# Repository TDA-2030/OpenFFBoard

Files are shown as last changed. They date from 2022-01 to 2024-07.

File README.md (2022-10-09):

# OpenFFBoard-ESP32S2 + VESC

这里将介绍使用 ESP32-S2/S3 版本的 OpenFFBoard 搭配自制 VESC 驱动器使用的一个低成本实现直驱力反馈方向盘方案。[OpenffBoard](https://github.com/Ultrawipf/OpenFFBoard) 是一个开源的力反馈方向盘的项目，整个项目硬件分为 `控制板` 和 `电机驱动板` 两个部分，这里对两个部分都进行了低成本方向的修改。

## 文件结构

```
├── LICENSE                <- 开源协议 >
├── Simple-BLDC            <- 电机驱动板 >
├── openffboard-esp32s2    <- OpenFFBoard 主控板 >
├── Structural_parts       <- 一些可能有帮助的结构件>
└── README.md              <- 此文件 >
```

## OpenFFBoard-ESP32S2 控制板

原项目控制板是 STM32F4 做主控，这里将主控换成了[乐鑫](https://www.espressif.com/zh-hans)的 ESP32-S2/S3 芯片，成本得到极大的降低，同时提供了 WiFi 的连接能力（虽然现在并没有用上）。硬件开源资料见 [openffboard-esp32s2](./openffboard-esp32s2)

> V1.1 版本的硬件支持 ESP32-S2 和 ESP32-S3 二选一焊接，下文统称为 ESP32

和原项目相比，ESP32 不能提供足够多的 GPIO ，所以按键输入和模拟输入通道数均从原来的 8 通道精简到了 4 通道。详细信息见原理图 [esp32s2-openffb.pdf](openffboard-esp32s2/esp32s2-openffb.pdf)。
ESP32 控制板的源码已提交 Pull Request 到原项目，支持的功能以及进度见 [PR](https://github.com/Ultrawipf/OpenFFBoard/pull/46)。

### 控制板固件烧录

参见[快速下载固件指南](https://github.com/TDA-2030/OpenFFBoard/tree/feature/add_esp32s2/Firmware/Targets/ESP32SX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)

## 电机驱动板

为了造福广大劳动人民，针对原项目的电机驱动我也进行了低成本的改造，原项目是采用了比较贵的 TMC4761 专用 FOC 控制芯片，我将著名的开源电调 [VESC](https://vesc-project.com/) 进行了魔改，去掉了昂贵的 DRV8301 芯片，用多个芯片实现了这一个芯片的功能。集成度下降了，但是价格更友好。魔改后的 VESC 我叫它 `Simple-BLDC` 。关于电机驱动板的更多信息见 [Simple-BLDC](Simple-BLDC/README.md)

## 组装好的样子

assembly

## 测试工具

[WheelTest](./WheelTest.rar) 提供了一个测试力反馈功能是否正常的软件

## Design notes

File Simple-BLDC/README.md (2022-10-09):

# Simple-BLDC

```
 _____ _                 _       ______ _    ______  _____ 
/  ___(_)               | |      | ___ \ |   |  _  \/  __ \
\ `--. _ _ __ ___  _ __ | | ___  | |_/ / |   | | | || /  \/
 `--. \ | '_ ` _ \| '_ \| |/ _ \ | ___ \ |   | | | || |    
/\__/ / | | | | | | |_) | |  __/ | |_/ / |___| |/ / | \__/\
\____/|_|_| |_| |_| .__/|_|\___| \____/\_____/___/   \____/
                  | |                                      
                  |_|                                      
```

Simple-BLDC 是基于 VESC6 的一个低成本实现方案，在硬件上兼容 VESC6 的固件

## 特点

- 超低成本
- 60mm x 60mm 双面板
- 元件单面布局
- 新增制动电阻功能
- USB Type-C 接口

## 参数

1. 输入电压：12V - 36V
2. 电机电流：50A
3. 编码器支持：AS5047（SPI接口）、ABI编码器
4. 通信接口：CAN总线接口、UART

## 固件源码

板子兼容[原版固件](https://github.com/vedderb/bldc)，专门适配的固件新增了制动电阻功能，你可以在 [bldc](https://github.com/TDA-2030/bldc/tree/hw_simple_bldc) 中看到对应的源代码。如何编译固件请参考[这里](https://github.com/TDA-2030/bldc/tree/hw_simple_bldc#prerequisites)，目前只提供在 linux 和 MacOS 编译的说明，Windows 编译会麻烦一些需要自行想办法。

## 上位机工具 VESC-TOOL

固件对应的 VESC-TOOL 版本为 `3.01`，在此[下载](./vesc_tool_3.01.exe)

## 制动电阻功能

原版的 VESC 是为电池设备设计的，所以是再生制动的方式，为了适应常见的开关电源，我加上了制动电阻来消耗再生制动的能量，防止开关电源超压损坏。
该功能需要在板子背面焊接上一个功率电阻，如下图：

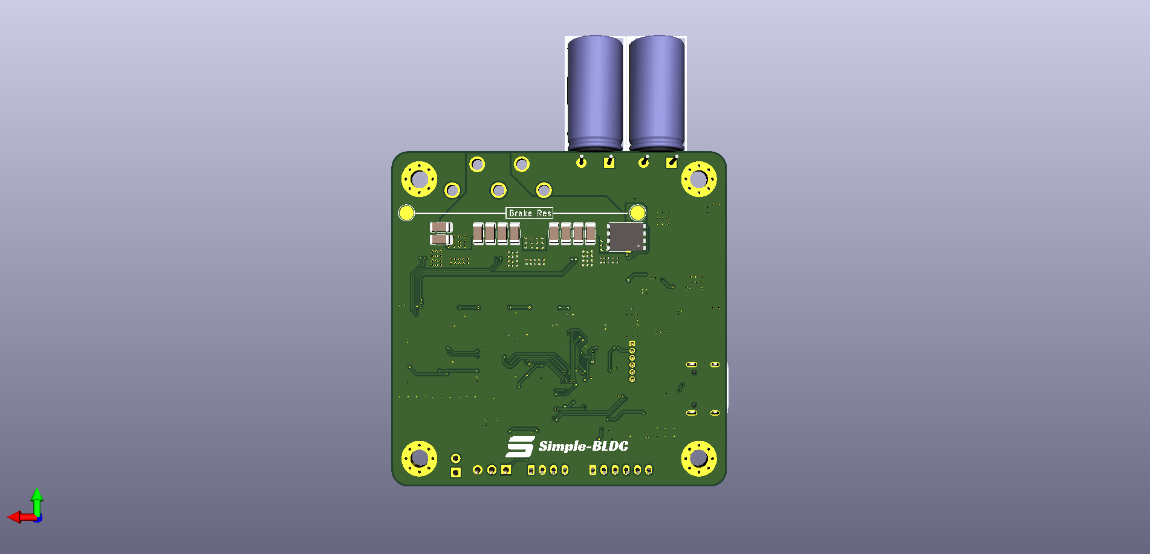
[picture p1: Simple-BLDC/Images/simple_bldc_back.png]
simple_bldc_back


电阻阻值一般为 1Ω 或 2Ω。

> 注意：制动电阻功能是在有点笨的保持电压在电机空闲时的输入电压，所以当电机在运行，并且你的输入电压在升高，那么制动电阻将会从电源消耗电流，电流值与变化的电压差值成正比。

制动电阻功能可以在 VESC-TOOL 进行开关选择，如下图：

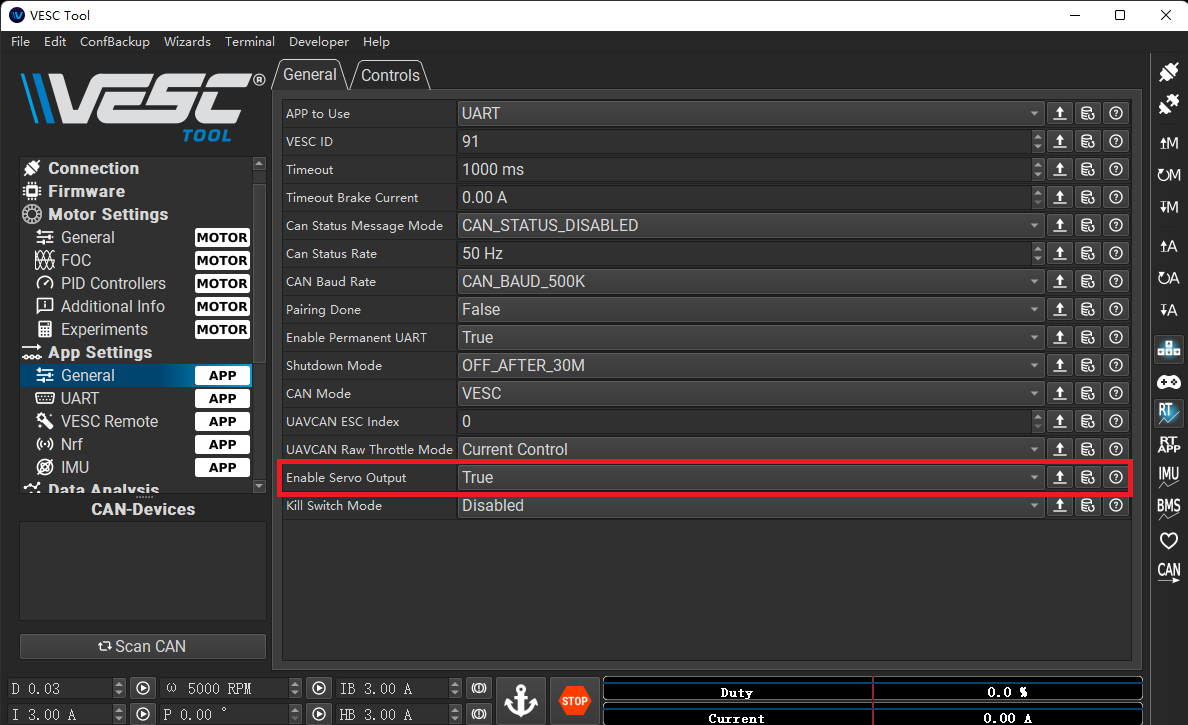
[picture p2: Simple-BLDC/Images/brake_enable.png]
brake_enable


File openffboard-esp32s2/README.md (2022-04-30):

## Preview image

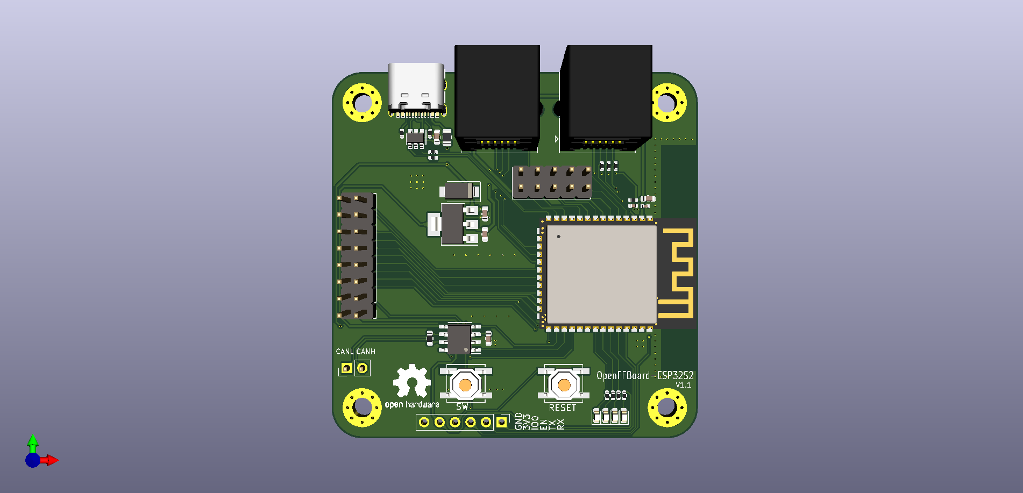
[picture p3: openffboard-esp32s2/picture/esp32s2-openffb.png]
front


## Known issues

The silk screen of the two buttons is wrong

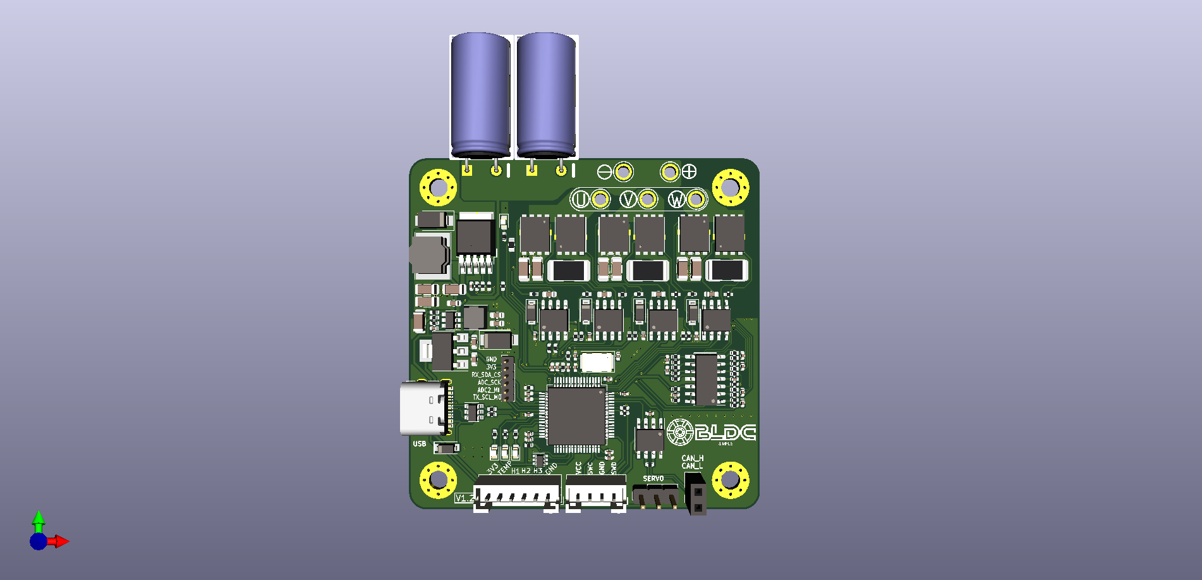
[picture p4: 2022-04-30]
Simple-BLDC/Images/simple_bldc.png

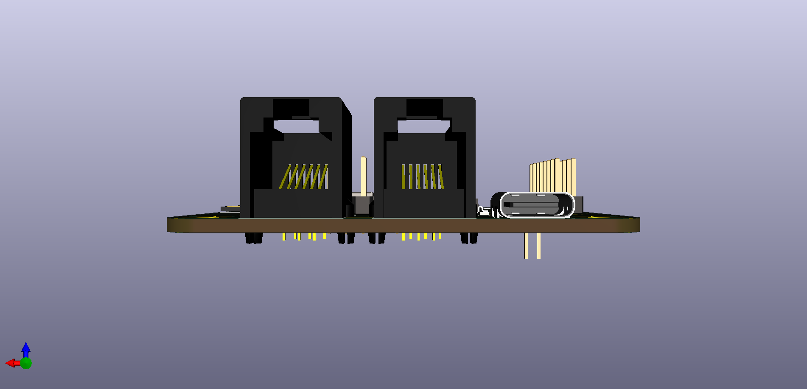
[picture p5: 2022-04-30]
openffboard-esp32s2/picture/connector.png

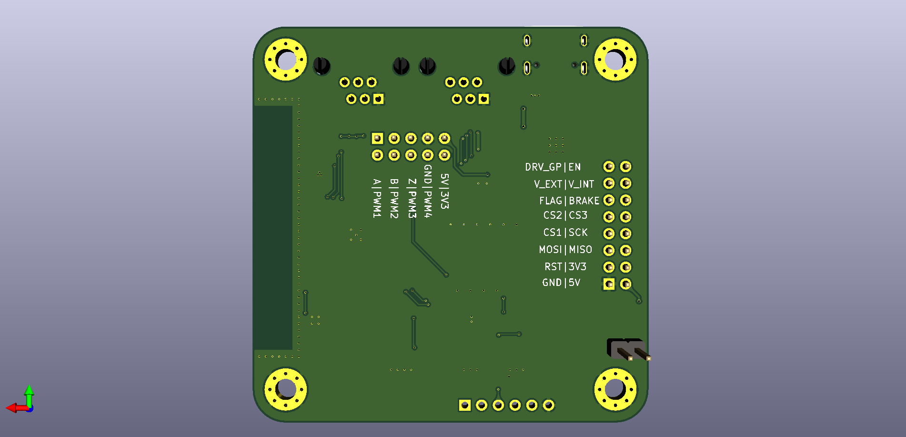
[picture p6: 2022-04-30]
openffboard-esp32s2/picture/back.png

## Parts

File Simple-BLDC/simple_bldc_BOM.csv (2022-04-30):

Comment | Description | Designator | Footprint | LibRef | Pins | Quantity | PartNumber | url
100n | desc | C1,C4,C5,C9,C15,C37,C45, | C_0402_1005Metric | libref | 2 | 7
2.2u | desc | C3,C20,C22,C26,C33,C34,C36,C38,C40,C41,C42,C43,C44,C63, | C_0402_1005Metric | libref | 2 | 14
10uf | desc | C6,C10,C11,C16,C17, | C_0603_1608Metric | libref | 2 | 5
10uF, 50V | desc | C7,C29,C30,C31,C46,C47,C48, | C_1206_3216Metric | libref | 2 | 7
1nF | desc | C8,C13,C18,C19,C23,C24, | C_0402_1005Metric | libref | 2 | 6
22uF, 25V | desc | C12,C14,C60, | C_1206_3216Metric | libref | 2 | 3
220n | desc | C21,C25,C27,C64, | C_0603_1608Metric | libref | 2 | 4
15p | desc | C35,C39, | C_0402_1005Metric | libref | 2 | 2
33nF | desc | C50, | C_0402_1005Metric | libref | 2 | 1
B5819W | desc | D1,D6,D7,D8,D11, | D_SOD-123 | libref | 2 | 5
RED | desc | D2, | LED_0603_1608Metric | libref | 2 | 1
GREEN | desc | D3, | LED_0603_1608Metric | libref | 2 | 1
BLUE | desc | D4, | LED_0603_1608Metric | libref | 2 | 1
SS210 | desc | D5, | D_SMA | libref | 2 | 1
SMAJ5.0CA_400W_5V | desc | D10, | D_SMA | libref | 2 | 1
LED_RED | desc | D12, | LED_0603_1608Metric | libref | 2 | 1
Logo | desc | H9, | simple-bldc-logo1 | libref | 0 | 1
6.8uH | desc | L1, | L_Taiyo-Yuden_NR-40xx | libref | 2 | 1
100uH | desc | L2, | L_Taiyo-Yuden_NR-60xx_HandSoldering | libref | 2 | 1
BSC030N08NS5 | desc | Q1,Q2,Q3,Q4,Q5,Q6, | DFN5_5x6_1.27P_(SO-8FL) | libref | 10 | 6
2k2 | desc | R1,R3,R6,R19,R37,R39,R41, | R_0402_1005Metric | libref | 2 | 7
120k | desc | R2,R21, | R_0402_1005Metric | libref | 2 | 2
10R | desc | R4,R42,R43,R45,R46,R48,R49, | R_0402_1005Metric | libref | 2 | 7
39k | desc | R5,R36,R38,R40, | R_0402_1005Metric | libref | 2 | 4
22R | desc | R7,R8, | R_0402_1005Metric | libref | 2 | 2
1k | desc | R9,R10,R11,R16,R23,R24,R25,R26,R32,R33,R34,R35,R57, | R_0402_1005Metric | libref | 2 | 13
120R | desc | R12,R52,R56, | R_0402_1005Metric | libref | 2 | 3
10k | desc | R13,R14,R15,R51,R55, | R_0402_1005Metric | libref | 2 | 5
22k | desc | R17, | R_0402_1005Metric | libref | 2 | 1
20k | desc | R18,R20,R22,R27,R28,R29,R30,R31, | R_0402_1005Metric | libref | 2 | 8
0.001R | desc | R44,R47,R50, | R_2512_Yageo_big_pads | libref | 2 | 3
MCP6024 | desc | U1, | SOIC-14_3.9x8.7mm_P1.27mm | libref | 14 | 1
MP1471 | desc | U2, | SOT-23-6 | libref | 6 | 1
XL7015 | desc | U3, | TO-252-5_TabPin3 | libref | 10 | 1
AMS1117-3.3 | desc | U4, | SOT-223-3_TabPin2 | libref | 4 | 1
IRS2101S | desc | U5,U6,U7,U11, | SOIC-8_3.9x4.9mm_P1.27mm | libref | 8 | 4
STM32F40X_LQFP64 | desc | U8, | LQFP-64_10x10mm_P0.5mm | libref | 64 | 1
TJA1051T-3 | desc | U9, | SOIC-8_3.9x4.9mm_P1.27mm | libref | 8 | 1
USBLC6-2SC6 | desc | U10, | SOT-23-6 | libref | 6 | 1
PESD3V3L5UY | desc | U12, | SOT-363_SC-70-6 | libref | 6 | 1
8MHz 10ppm (X50328MSB2GI) | desc | X1, | Crystal_SMD_5032-2Pin_5.0x3.2mm | libref | 2 | 1
Net-Tie_2 | desc | NT1,NT2,NT3,NT4,NT5,NT6, | NetTie-2_SMD_Pad0.5mm | libref | 2 | 6
NTC 10k | desc | NTC1, | R_0603_1608Metric | libref | 2 | 1
10uF, 50V | desc | C2,C49,C51,C52,C53,C54,C55,C57,C58,C59, | C_1206_3216Metric | libref | 2 | 10
Logo | desc | H5, | simple-bldc-logo3 | libref | 0 | 1
NTMFS4C08N | desc | Q7, | DFN5_5x6_1.27P_(SO-8FL) | libref | 10 | 1
POS | desc | RES1,RES2, | TestPoint_Pad_D2.5mm | libref | 1 | 2
Through Hole Items
330u, 63V | desc | C28,C32, | CP_10x20mm_hor_with_model_brd_edge | libref | 2 | 2
MountingHole_Pad | desc | H1,H2,H3,H4, | MountingHole_3.2mm_M3_Pad_Via | libref | 9 | 4
Conn_01x03 | desc | J1, | PinHeader_1x03_P2.54mm_Vertical | libref | 3 | 1
USB_C_Receptacle_USB2.0 | desc | J2, | USB_C_Receptacle_Palconn_UTC16-G | libref | 22 | 1
CAN | desc | J3, | PinSocket_1x02_P2.54mm_Vertical | libref | 2 | 1
Conn_01x06 | desc | J4, | PinHeader_1x06_P1.27mm_Vertical | libref | 6 | 1
SWD | desc | J6, | JST_PH_B4B-PH-K_1x04_P2.00mm_Vertical | libref | 4 | 1
HALL/Encoder | desc | P1, | JST_PH_B6B-PH-K_1x06_P2.00mm_Vertical | libref | 6 | 1
MOTOR1 | desc | P2,P3,P4, | 1pin_2mm | libref | 1 | 3
MOTOR3 | desc | NEG1, | 1pin_2mm | libref | 1 | 1
POS | desc | POS1, | 1pin_2mm | libref | 1 | 1

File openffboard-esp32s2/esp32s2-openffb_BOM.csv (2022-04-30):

Comment | Description | Designator | Footprint | LibRef | Pins | Quantity | PartNumber | url
10uf | desc | C1,C2,C3,C4,C19, | C_0603_1608Metric | libref | 2 | 5
0.1uf | desc | C6,C15, | C_0402_1005Metric | libref | 2 | 2
SMAJ5.0CA_400W_5V | desc | D1, | D_SMA | libref | 2 | 1
blue | desc | D9, | LED_0603_1608Metric | libref | 2 | 1
yellow | desc | D10, | LED_0603_1608Metric | libref | 2 | 1
red | desc | D11, | LED_0603_1608Metric | libref | 2 | 1
green | desc | D12, | LED_0603_1608Metric | libref | 2 | 1
500mA | desc | F1, | Fuse_0805_2012Metric | libref | 2 | 1
22Ω | desc | R1,R2, | R_0402_1005Metric | libref | 2 | 2
10k | desc | R4, | R_0402_1005Metric | libref | 2 | 1
5.1k | desc | R5,R10,R11,R12,R13, | R_0402_1005Metric | libref | 2 | 5
1k | desc | R6,R7,R8,R9, | R_0402_1005Metric | libref | 2 | 4
120Ω | desc | R15, | R_0603_1608Metric | libref | 2 | 1
AMS1117-3.3 | desc | U1, | SOT-223-3_TabPin2 | libref | 4 | 1
ESP32-S3-WROOM-1 | desc | U2, | ESP32-S3-WROOM-1 | libref | 49 | 1
TJA1051T-3 | desc | U3, | SOIC-8_3.9x4.9mm_P1.27mm | libref | 8 | 1
USBLC6-2SC6 | desc | U4, | SOT-23-6 | libref | 6 | 1
ESP32-S2-SOLO | desc | U5, | ESP32-S2-SOLO | libref | 49 | 1
SW_Push | desc | SW1,SW2, | SW_SPST_EVPBF | libref | 4 | 2
logo | desc | logo1, | OSHW-Logo2_9.8x8mm_SilkScreen | libref | 0 | 1
Through Hole Items
MountingHole_Pad | desc | H1,H2,H3,H4, | MountingHole_3.2mm_M3_Pad_Via | libref | 9 | 4
USB_C_Receptacle_USB2.0 | desc | J1, | USB_C_Receptacle_Palconn_UTC16-G | libref | 22 | 1
Debug | desc | J2, | PinHeader_1x06_P2.54mm_Vertical | libref | 6 | 1
CAN_Connector | desc | J3, | PinHeader_1x02_P2.54mm_Vertical | libref | 2 | 1
Motor Driver | desc | J4, | PinHeader_2x08_P2.54mm_Vertical | libref | 16 | 1
ENCODER & PWM | desc | J5, | PinHeader_2x05_P2.54mm_Vertical | libref | 10 | 1
RJ12 | desc | J6,J7, | RJ25_Wayconn_MJEA-660X1_Horizontal | libref | 8 | 2

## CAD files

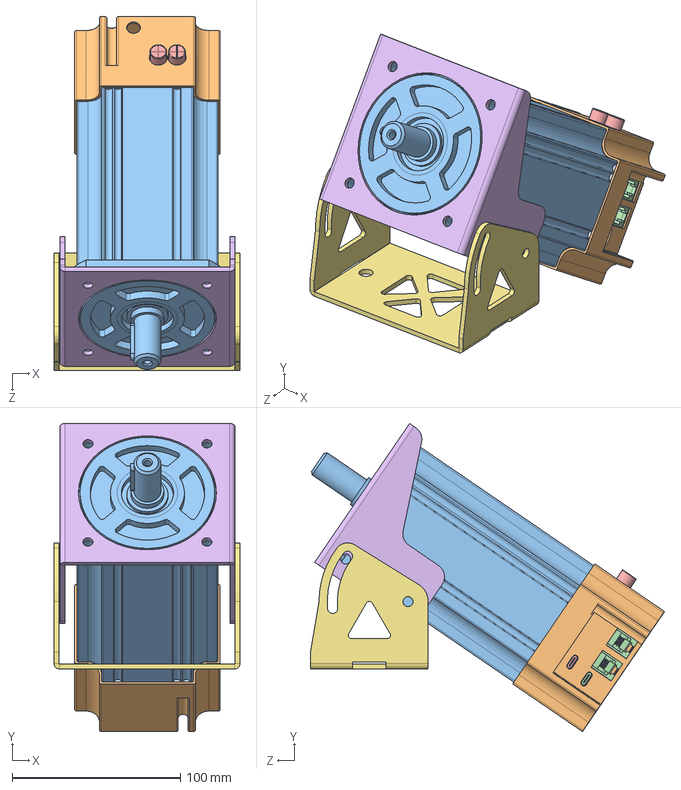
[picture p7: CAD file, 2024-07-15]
Structural_parts/ver4/方向盘主机.SLDASM
110.5 x 183.2 x 210.5 mm
层板
后盖
AC Servo motor 90ST-M04025 v1
esp32s2-openffb
simple_bldc
底座
底座1

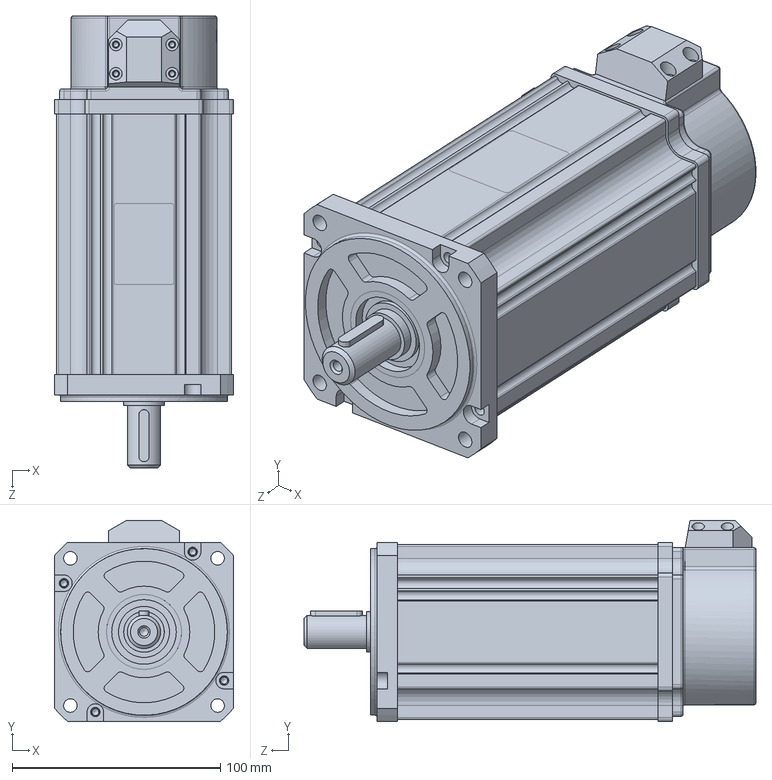
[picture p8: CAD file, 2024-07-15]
Structural_parts/ver4/AC Servo motor 90ST-M04025 v1.SLDASM
86.0 x 96.5 x 217.0 mm

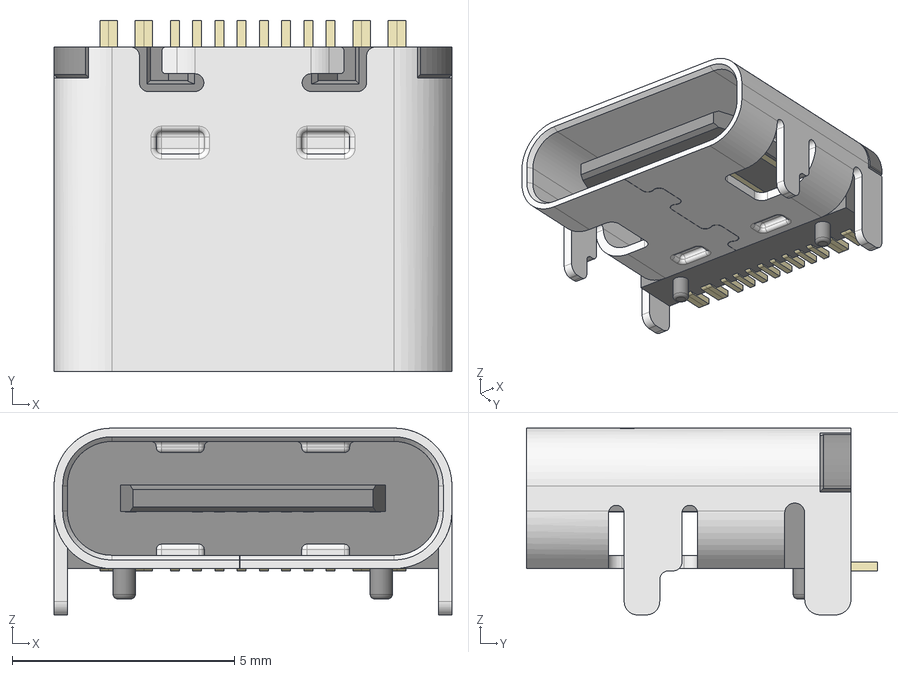
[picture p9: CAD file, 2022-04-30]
openffboard-esp32s2/HRO_TYPE-C-31-M-12.step
8.95 x 7.90 x 4.20 mm

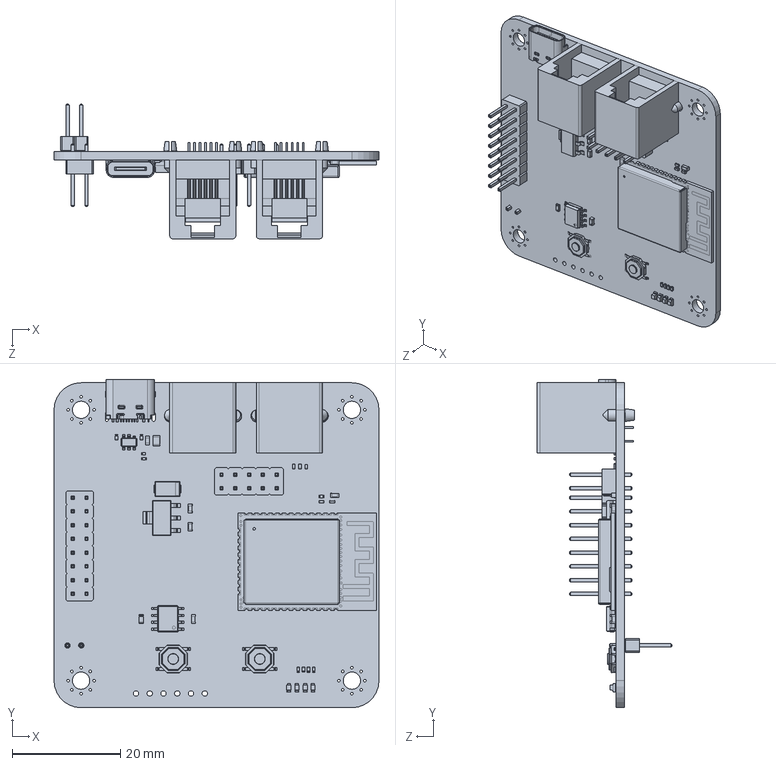
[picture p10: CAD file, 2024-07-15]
Structural_parts/ver4/esp32s2-openffb.SLDPRT
60.0 x 60.6 x 24.8 mm

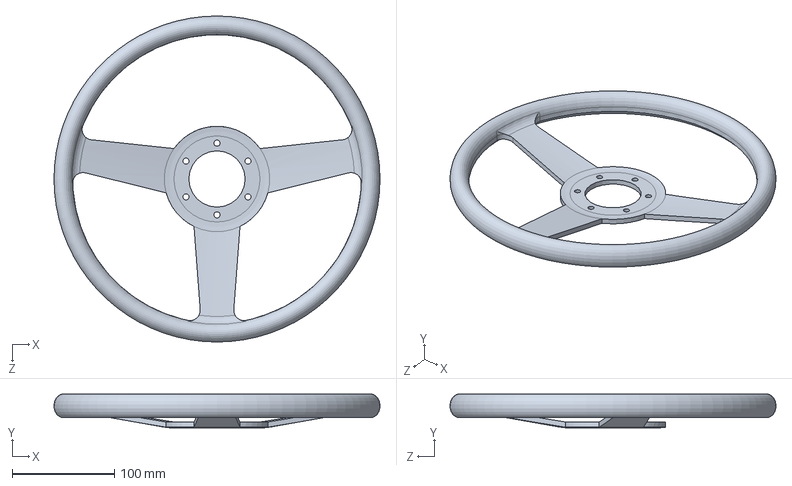
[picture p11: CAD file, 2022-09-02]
Structural_parts/wheel.SLDPRT
318.8 x 33.2 x 318.8 mm

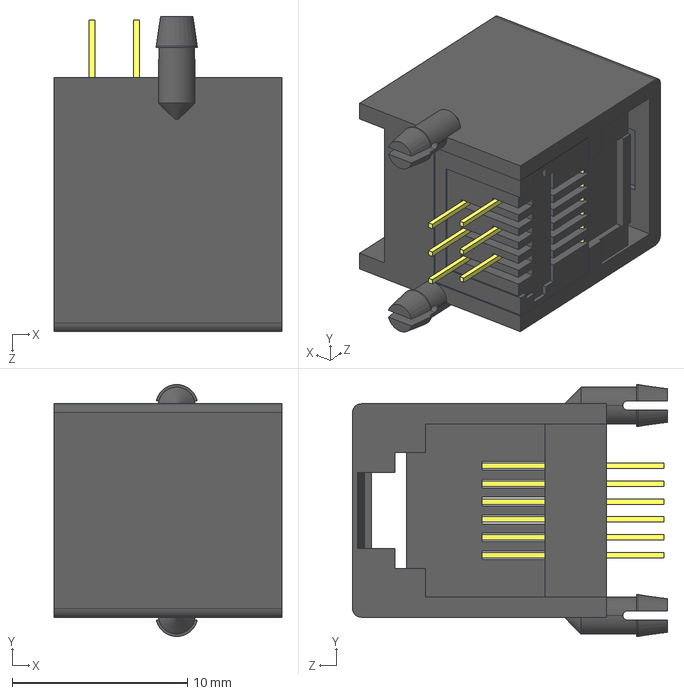
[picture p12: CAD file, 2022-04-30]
openffboard-esp32s2/RJ11-WE-HOR-TAB-UP.STEP
13.0 x 14.4 x 18.0 mm

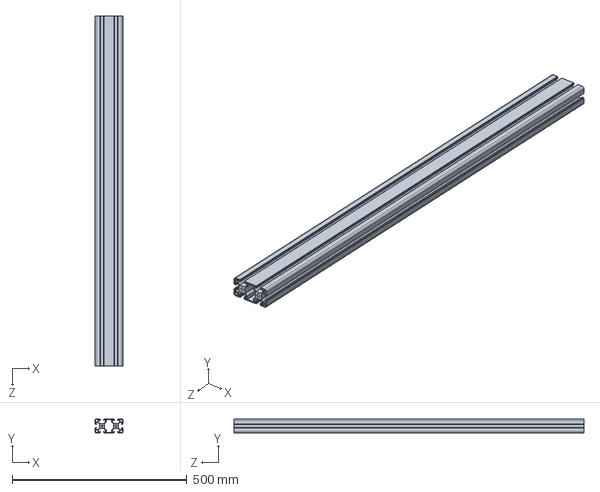
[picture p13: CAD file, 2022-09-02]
Structural_parts/4080-aluminum-profile-1m.SLDPRT
80.0 x 40.0 x 1000.0 mm

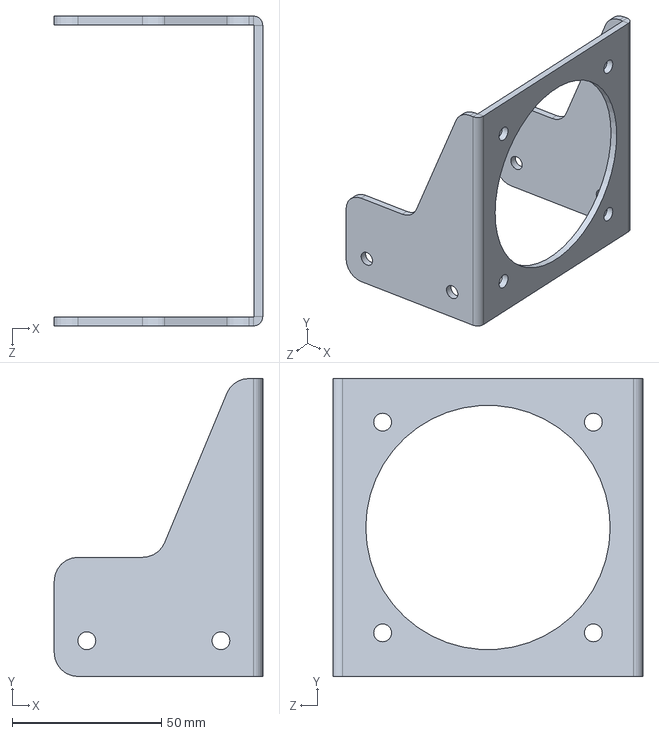
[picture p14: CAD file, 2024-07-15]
Structural_parts/ver4/底座.SLDPRT
70.0 x 100.0 x 104.0 mm

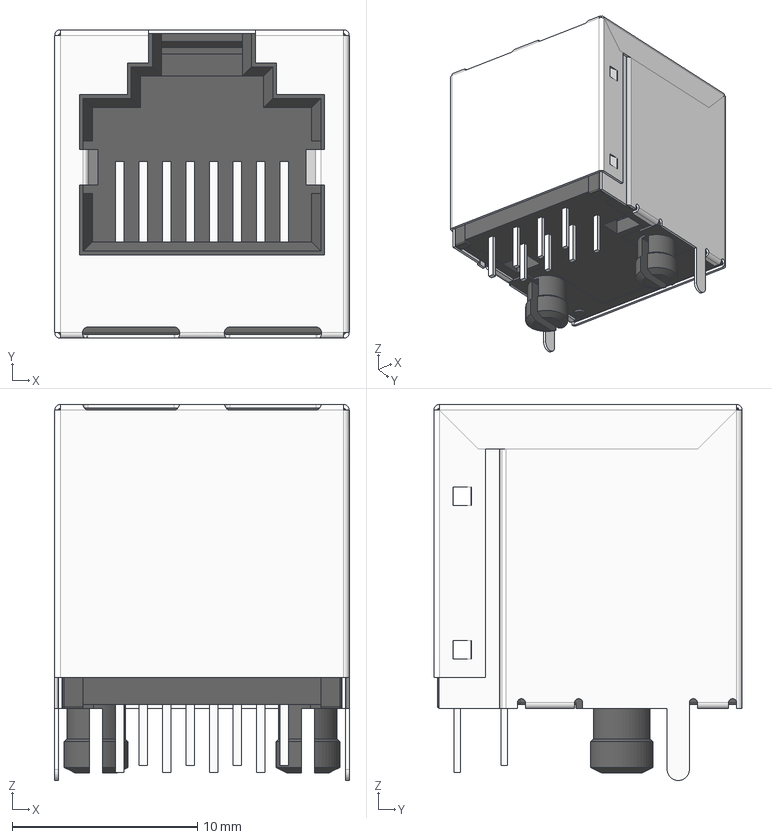
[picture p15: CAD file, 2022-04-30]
openffboard-esp32s2/RJ45-Jack.step
15.9 x 16.7 x 20.3 mm
RJ45 Lower Insert
RJ45 Odd Pins x 4
RJ45 Even Pins x 4
RJ45 Main Insert
RJ45 Shell

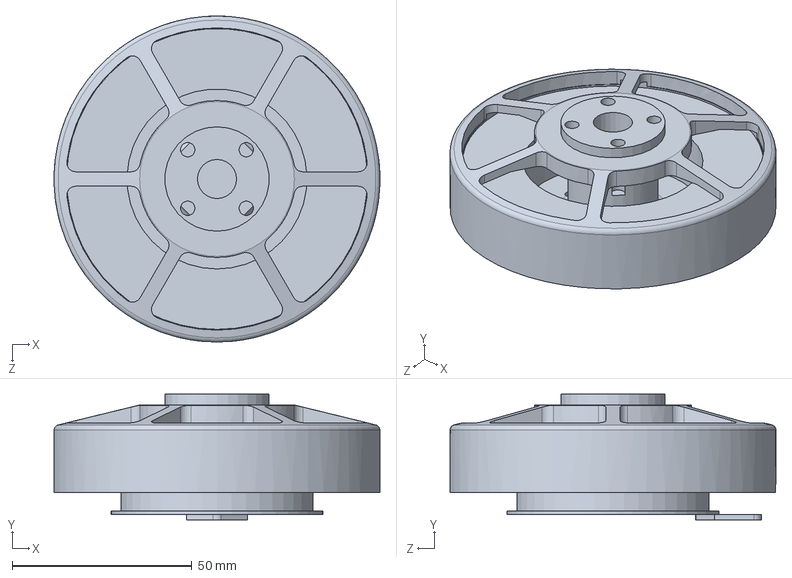
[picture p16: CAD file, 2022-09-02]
Structural_parts/bldc-motor-A12.SLDPRT
90.6 x 34.9 x 90.6 mm

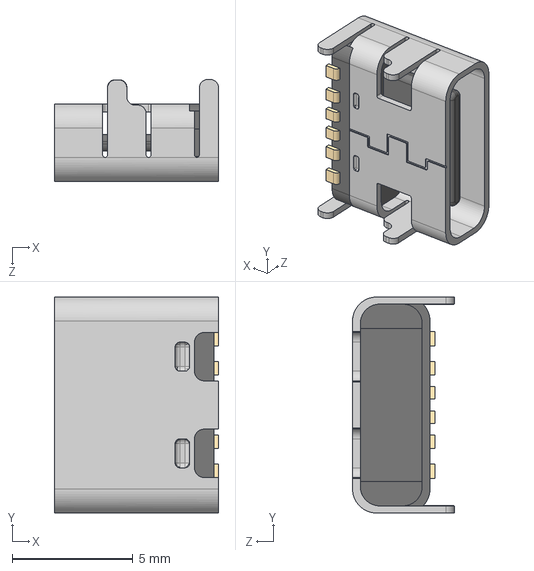
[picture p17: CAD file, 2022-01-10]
openffboard-esp32s2/USB_Type_C_6pin.STEP
6.80 x 8.94 x 4.22 mm

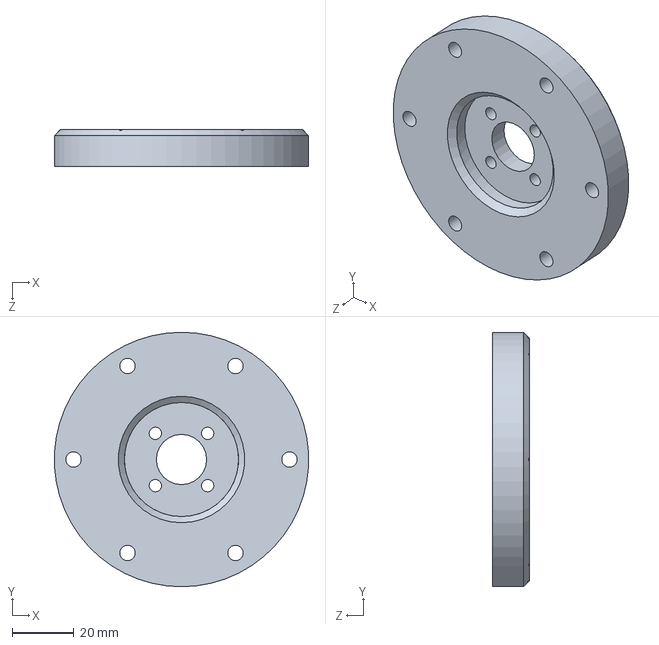
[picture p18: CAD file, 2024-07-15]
Structural_parts/ver4/快拆法兰.SLDPRT
82.4 x 82.5 x 12.0 mm

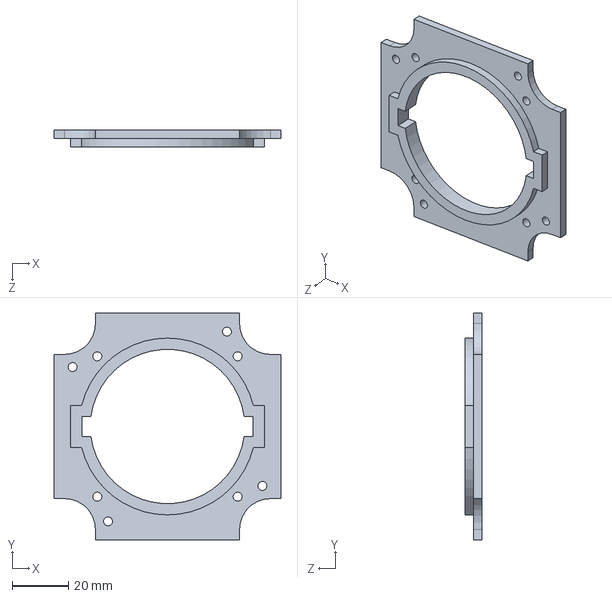
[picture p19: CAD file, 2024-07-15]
Structural_parts/ver4/层板.SLDPRT
80.9 x 80.9 x 6.00 mm

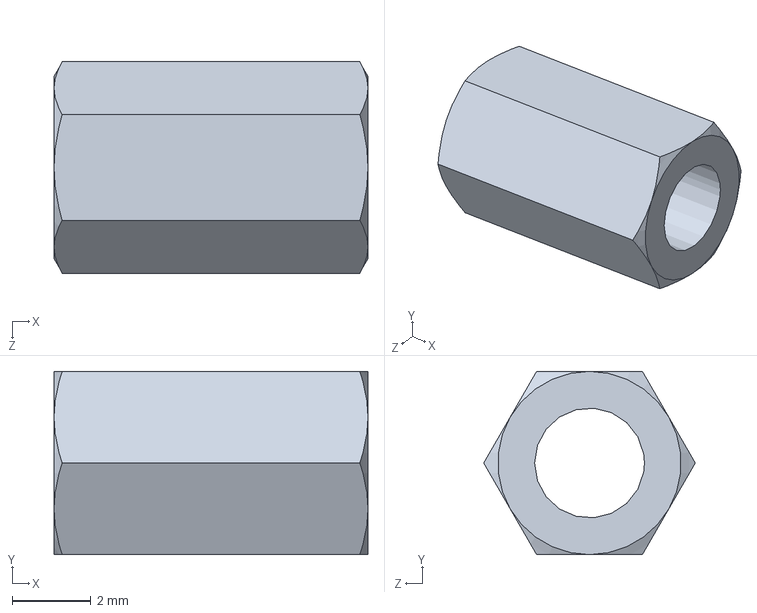
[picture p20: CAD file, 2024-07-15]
Structural_parts/ver4/六角铜柱1.SLDPRT
8.00 x 4.67 x 5.39 mm

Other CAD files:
Structural_parts/ver4/后盖.SLDPRT
Structural_parts/ver4/六角铜柱2.SLDPRT
Structural_parts/ver4/底座1.SLDPRT
Structural_parts/ver4/快拆法兰z11.SLDPRT
Structural_parts/ver1/falan.SLDPRT
Structural_parts/ver1/zhijia-2.SLDPRT
Structural_parts/ver1/zhijia-3.SLDPRT
Structural_parts/ver1/zhijia.SLDPRT
Structural_parts/ver1/zhijia.STEP
Structural_parts/ver1/zhijia.STL
Structural_parts/ver1/装配体1.SLDASM
Structural_parts/ver2/falan.SLDPRT
Structural_parts/ver2/支架-钣金.SLDPRT
Structural_parts/ver2/支架-钣金.STEP
Structural_parts/ver2/电机支架-钣金.SLDPRT
Structural_parts/ver2/电机支架-钣金.STEP
Structural_parts/ver2/装配体-钣金.SLDASM
Structural_parts/ver3/M3螺丝-7.6mm.SLDPRT
Structural_parts/ver3/M3螺帽.SLDPRT
Structural_parts/ver3/M3铜柱-11mm.SLDPRT
Structural_parts/ver3/M3铜柱-15mm.SLDPRT
Structural_parts/ver3/传感器支架.SLDPRT
Structural_parts/ver3/后面板.SLDPRT
Structural_parts/ver3/电机架-钣金.SLDPRT
Structural_parts/ver3/电机架-钣金.STEP
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

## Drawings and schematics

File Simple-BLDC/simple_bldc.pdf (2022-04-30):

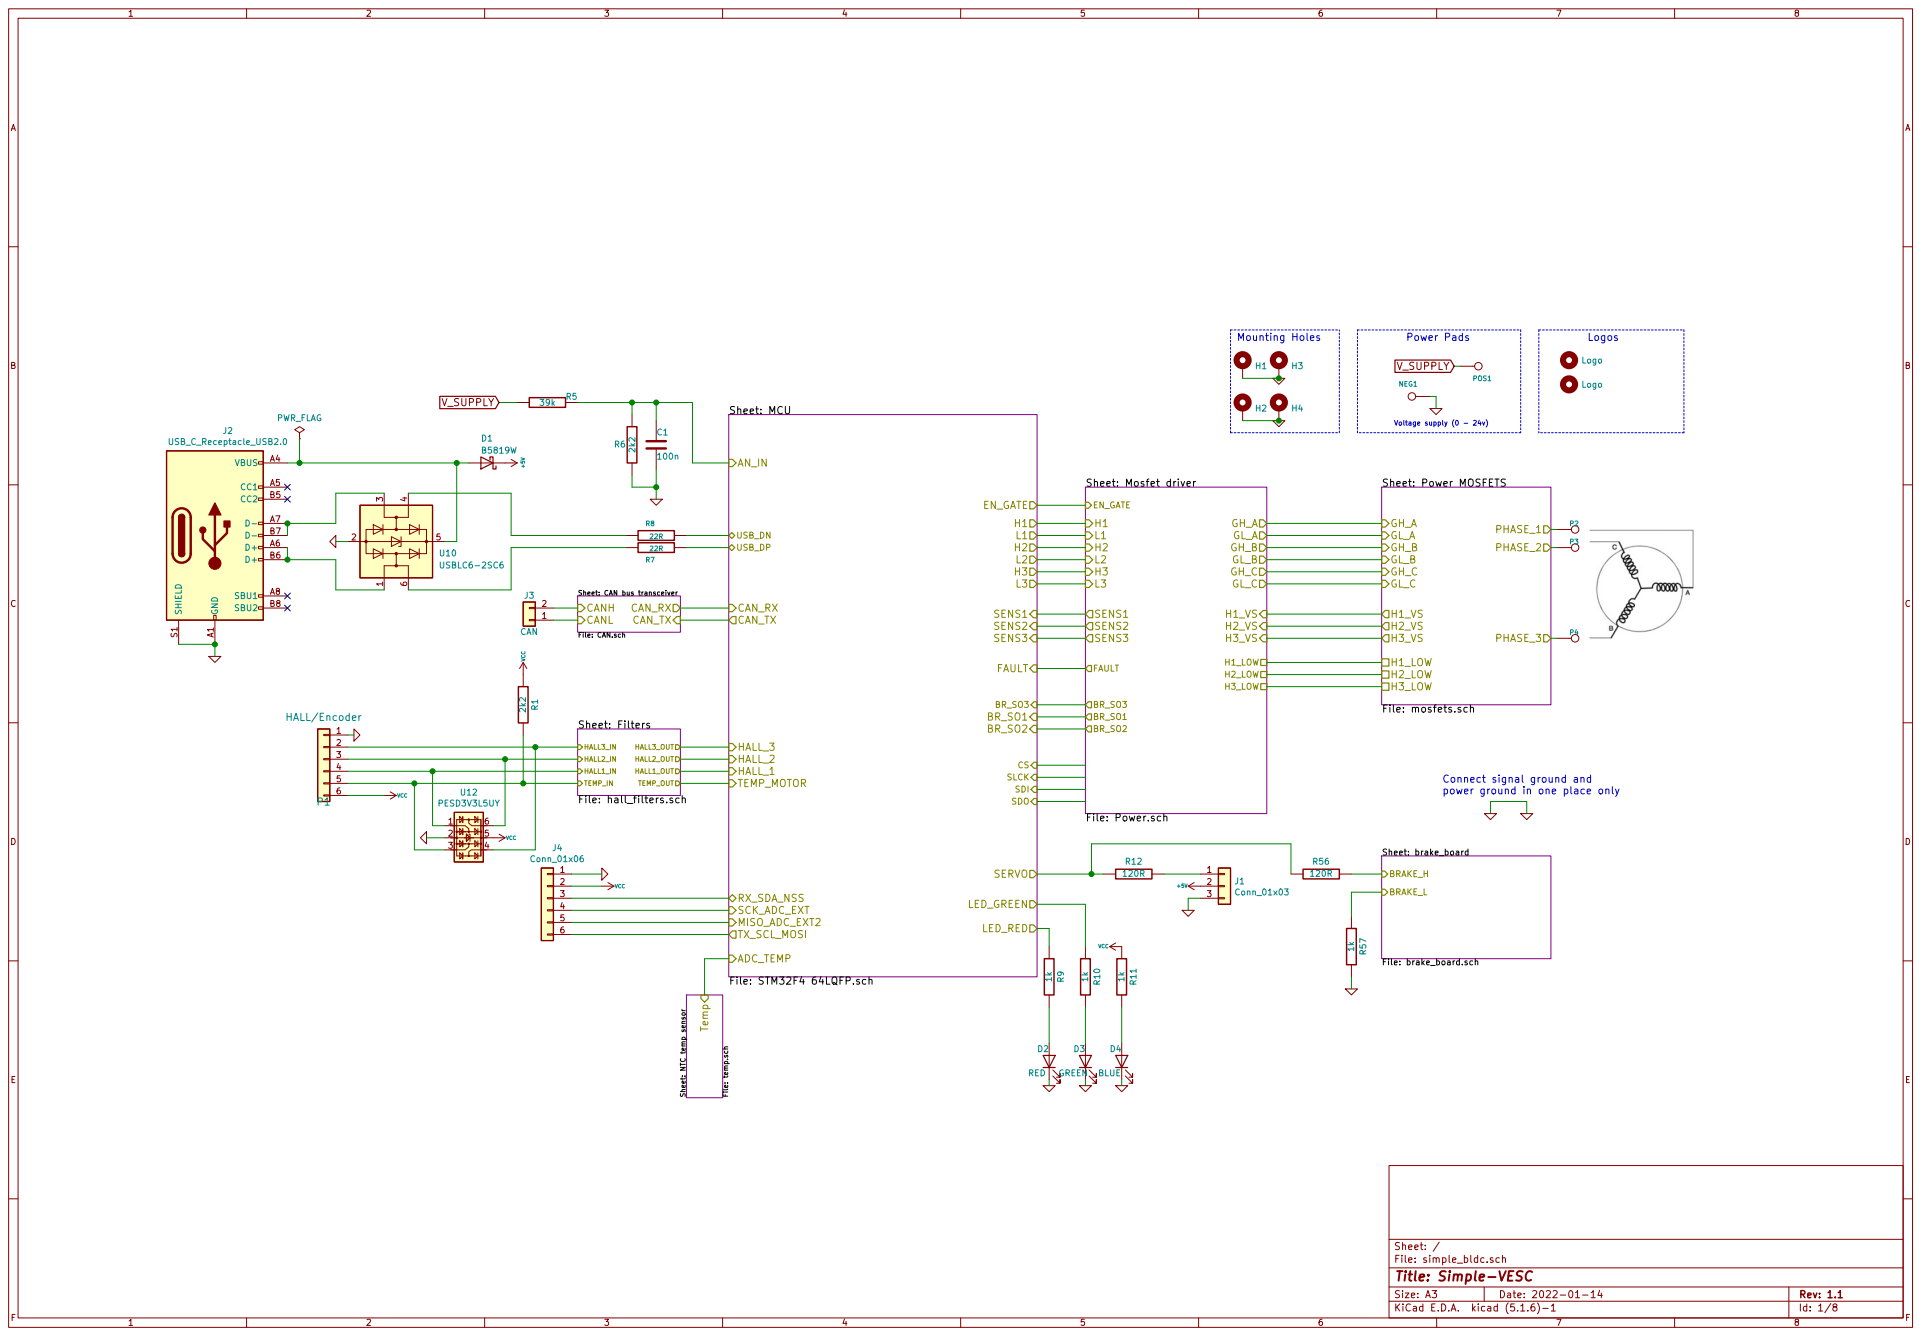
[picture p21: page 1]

Sheet: Mosfet driver File: Power.sch H1
FAULT EN_GATE
L1 FAULTH3 H2 H1 SENS3

power ground in one place only

File: simple_bldc.sch Sheet: /
Id: 1/8 Title: Simple-VESC

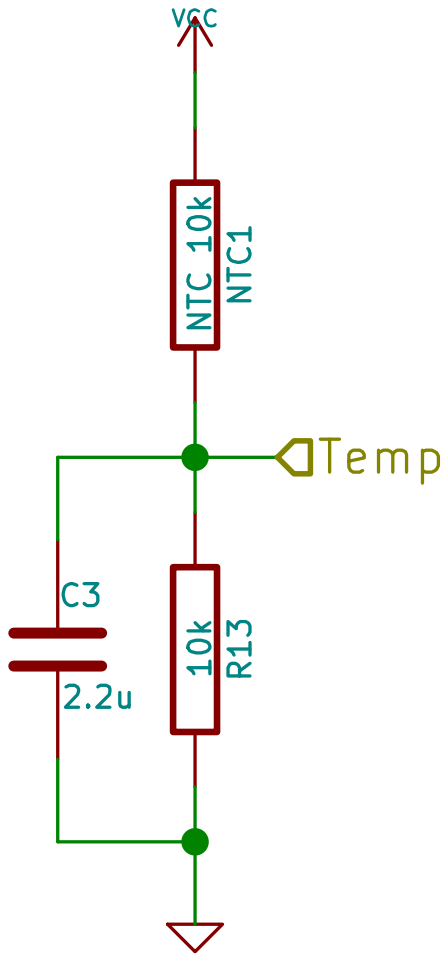
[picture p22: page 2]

Sheet: /NTC temp sensor/ 10k R13 C3

File: temp.sch
Id: 2/8 Title: Simple-VESC

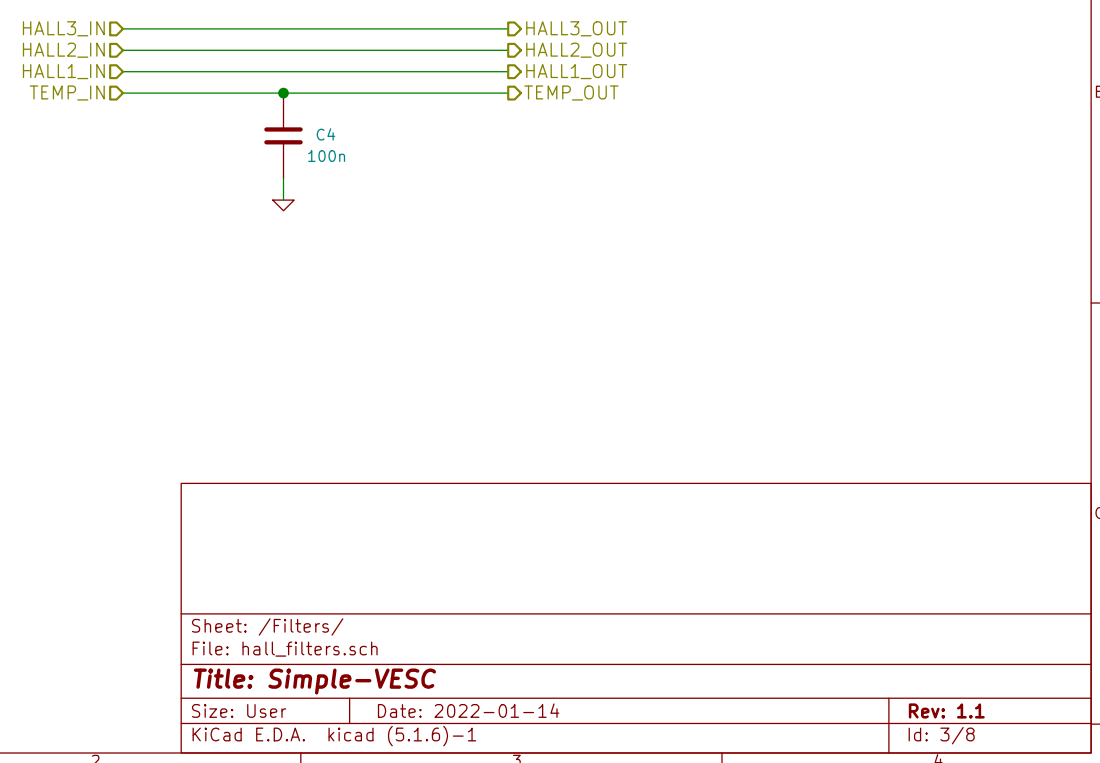
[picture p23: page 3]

Id: 3/8 Title: Simple-VESC

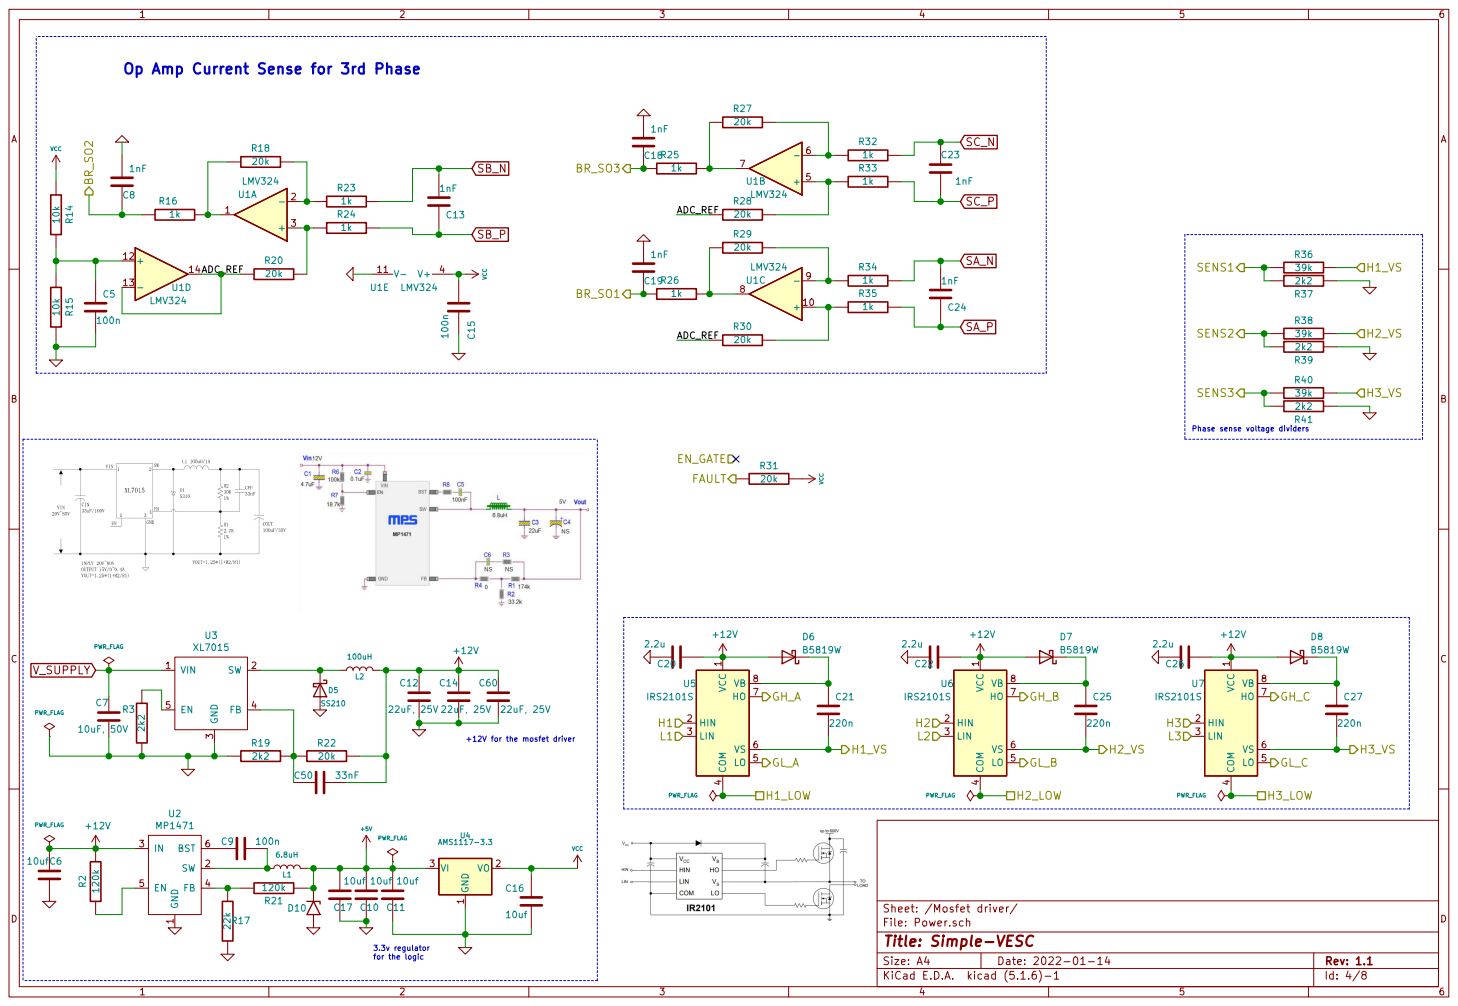
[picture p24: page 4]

File: Power.sch Sheet: /Mosfet driver/
Id: 4/8 Title: Simple-VESC

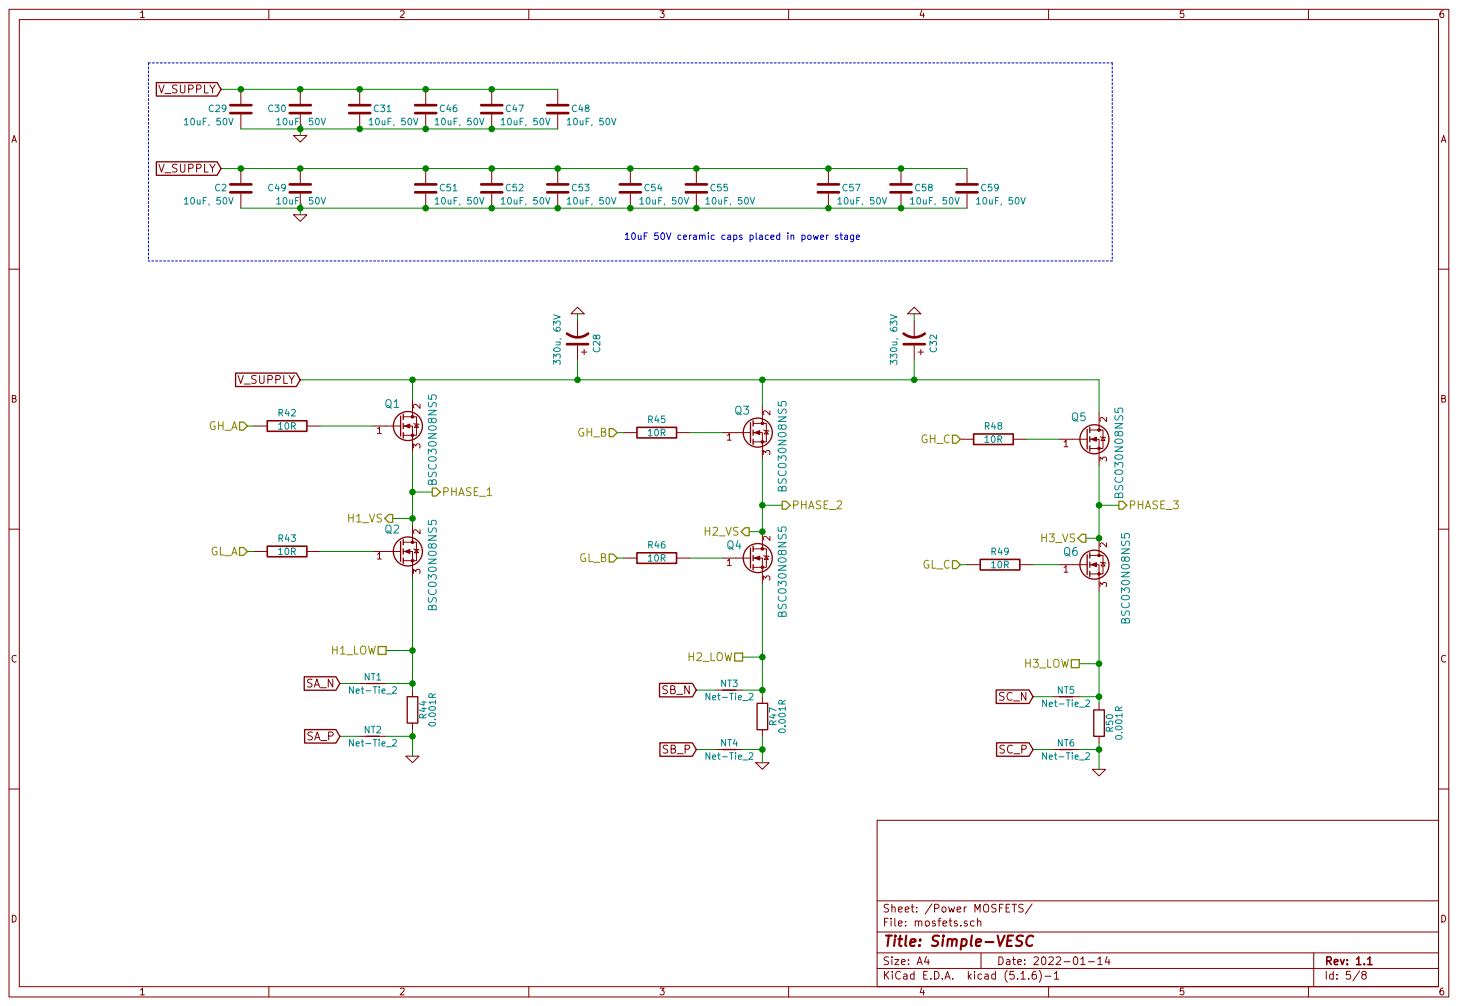
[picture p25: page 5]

10uF 50V ceramic caps placed in power stage

File: mosfets.sch Sheet: /Power MOSFETS/
Id: 5/8 Title: Simple-VESC

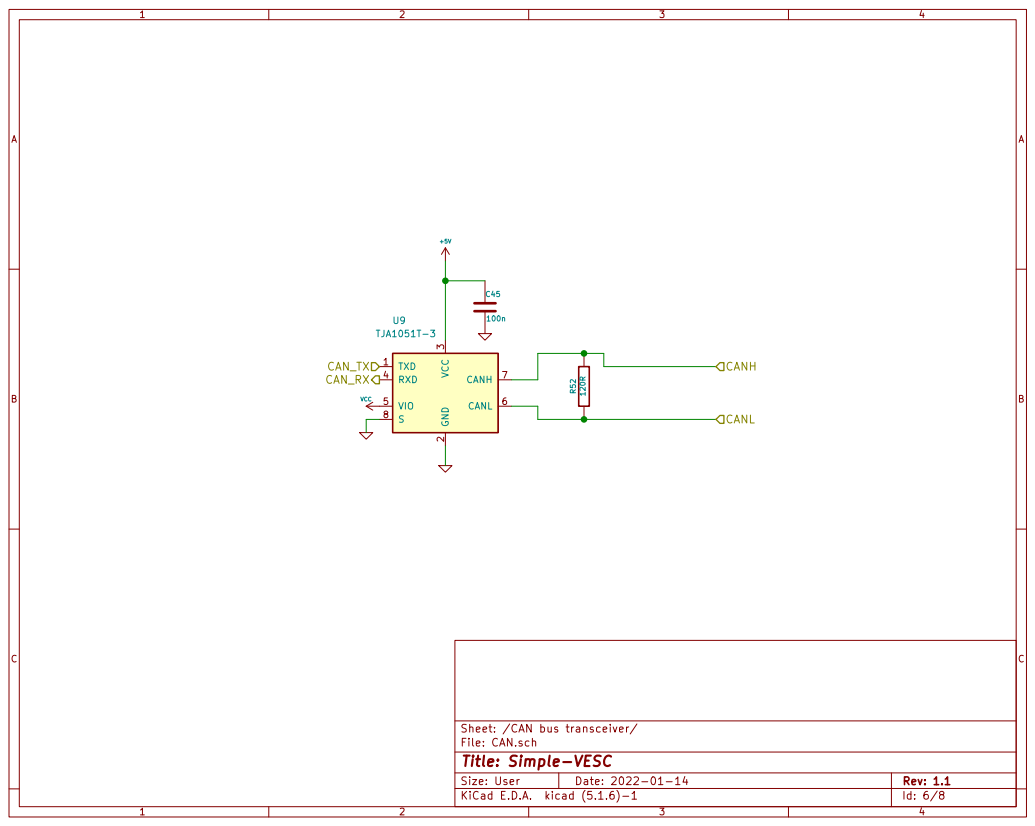
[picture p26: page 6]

3 RXD 4 VIO 5 CANL 6 CANH 7 S

Id: 6/8 Title: Simple-VESC

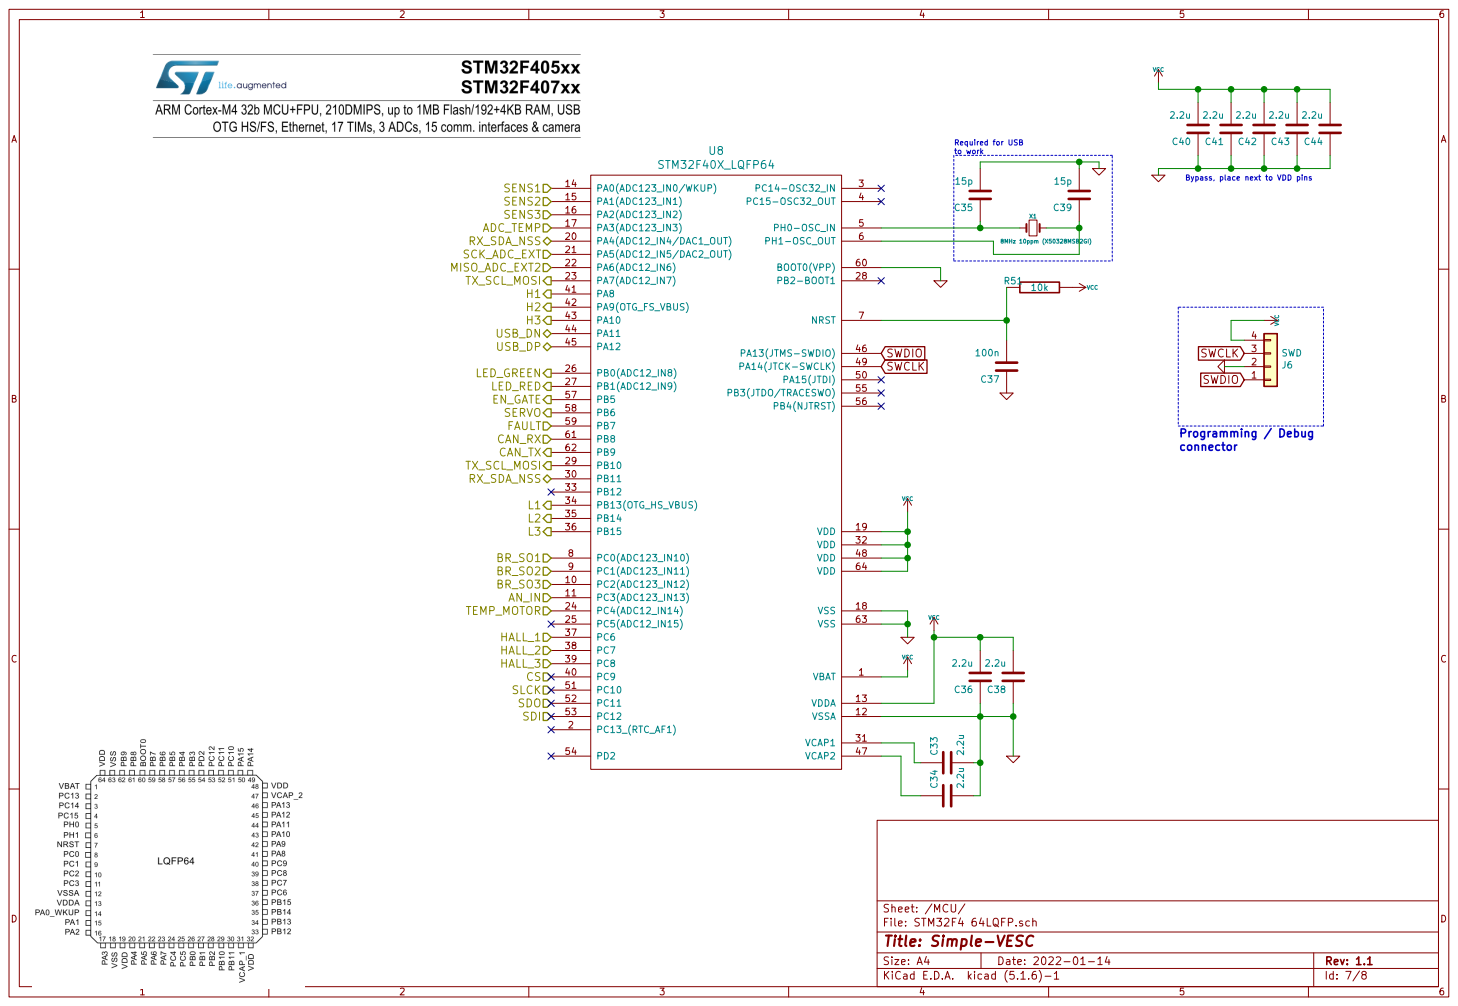
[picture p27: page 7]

connector Required for USB

File: STM32F4 64LQFP.sch Sheet: /MCU/
Id: 7/8 Title: Simple-VESC

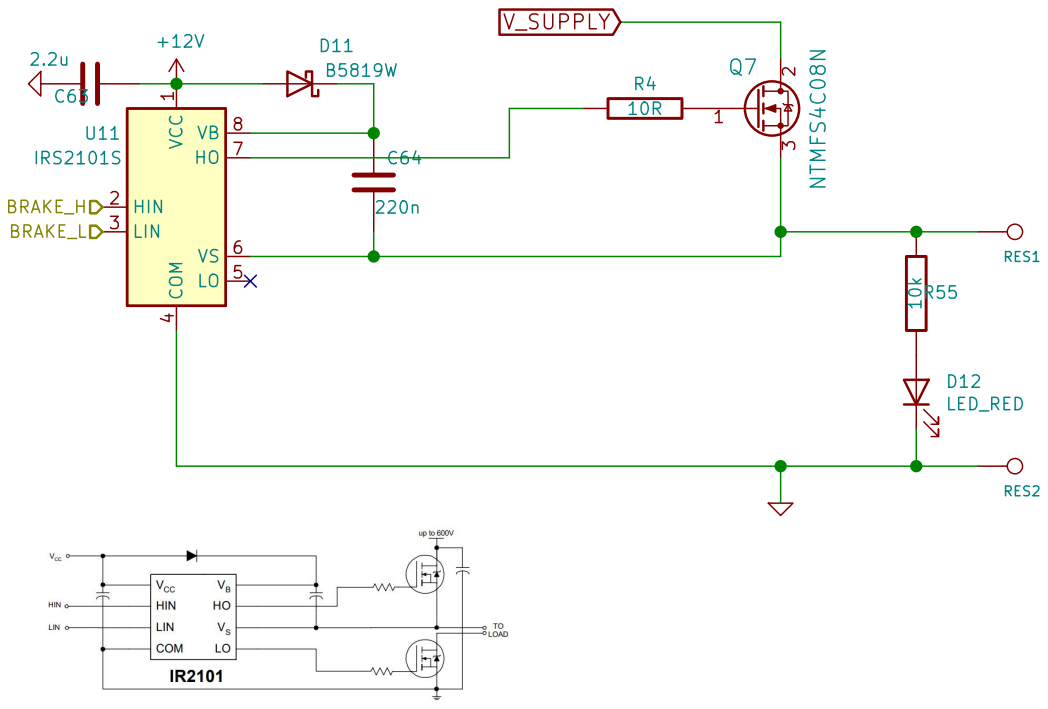
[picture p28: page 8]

File: brake_board.sch
Id: 8/8 Title: Brake-board

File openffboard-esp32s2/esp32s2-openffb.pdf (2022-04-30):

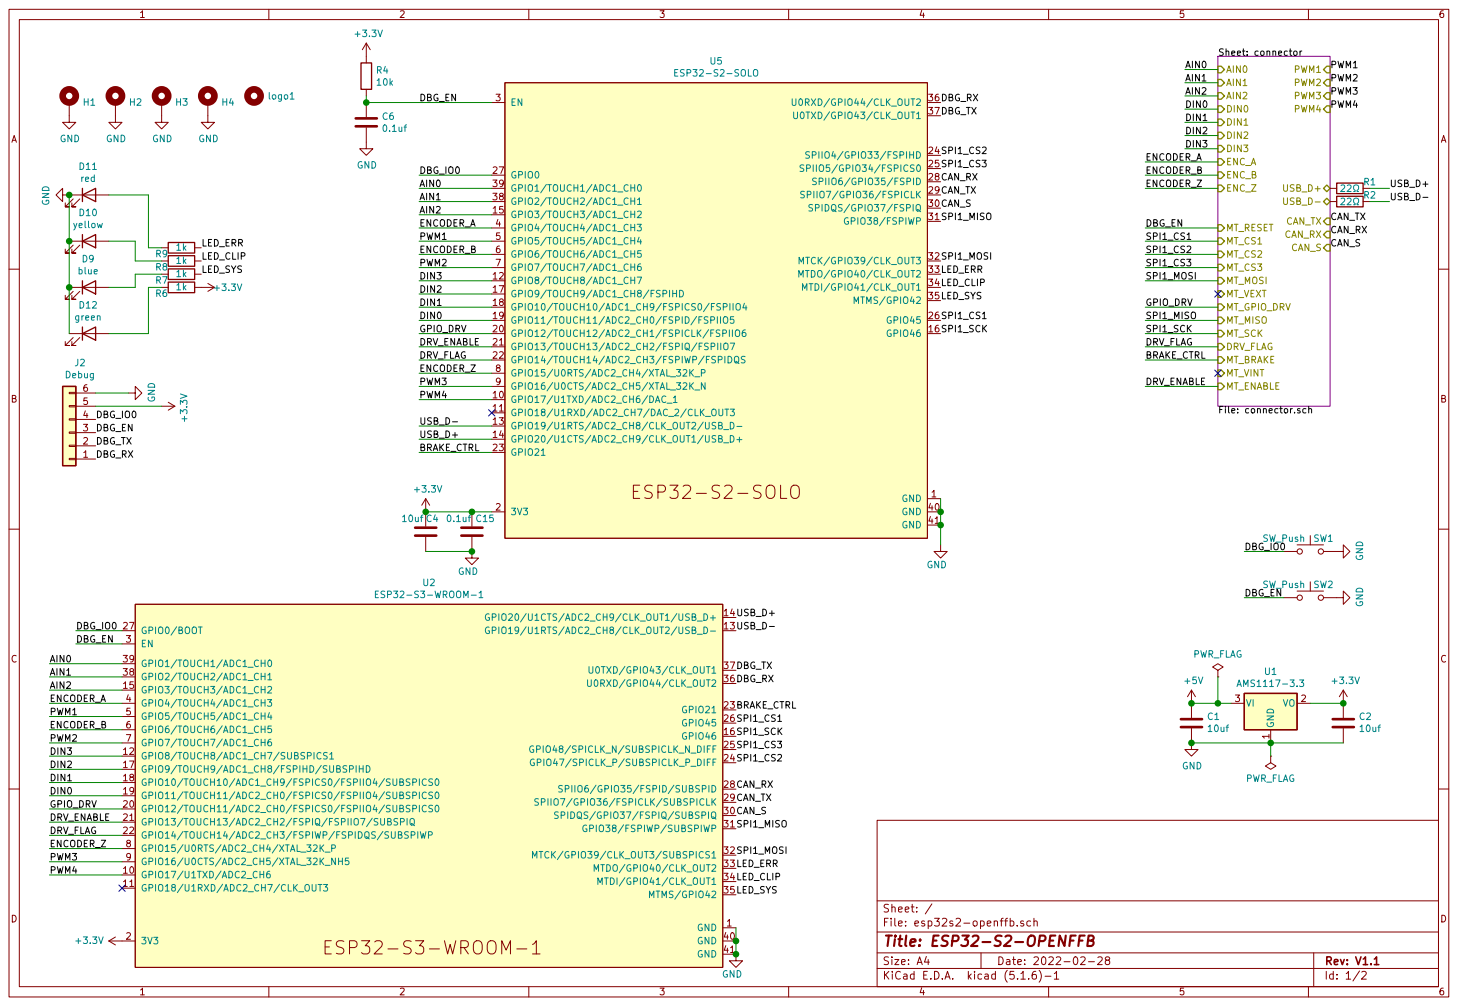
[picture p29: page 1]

File: esp32s2-openffb.sch Sheet: /
Id: 1/2 Title: ESP32-S2-OPENFFB

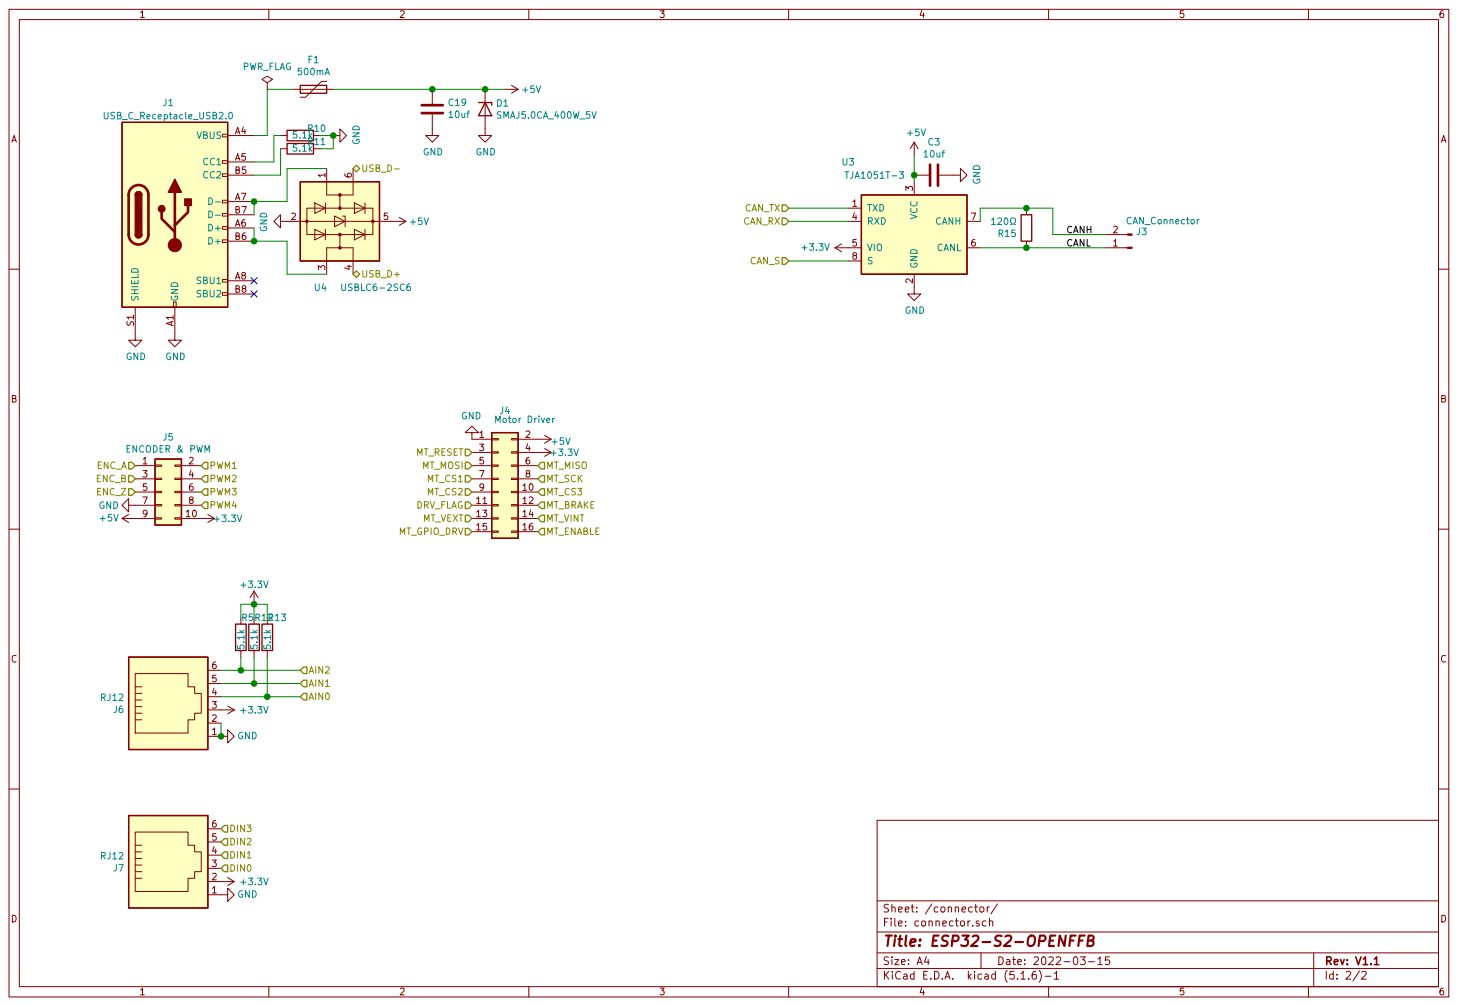
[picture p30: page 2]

3 RXD 4 VIO 5 CANL 6 CANH 7 S

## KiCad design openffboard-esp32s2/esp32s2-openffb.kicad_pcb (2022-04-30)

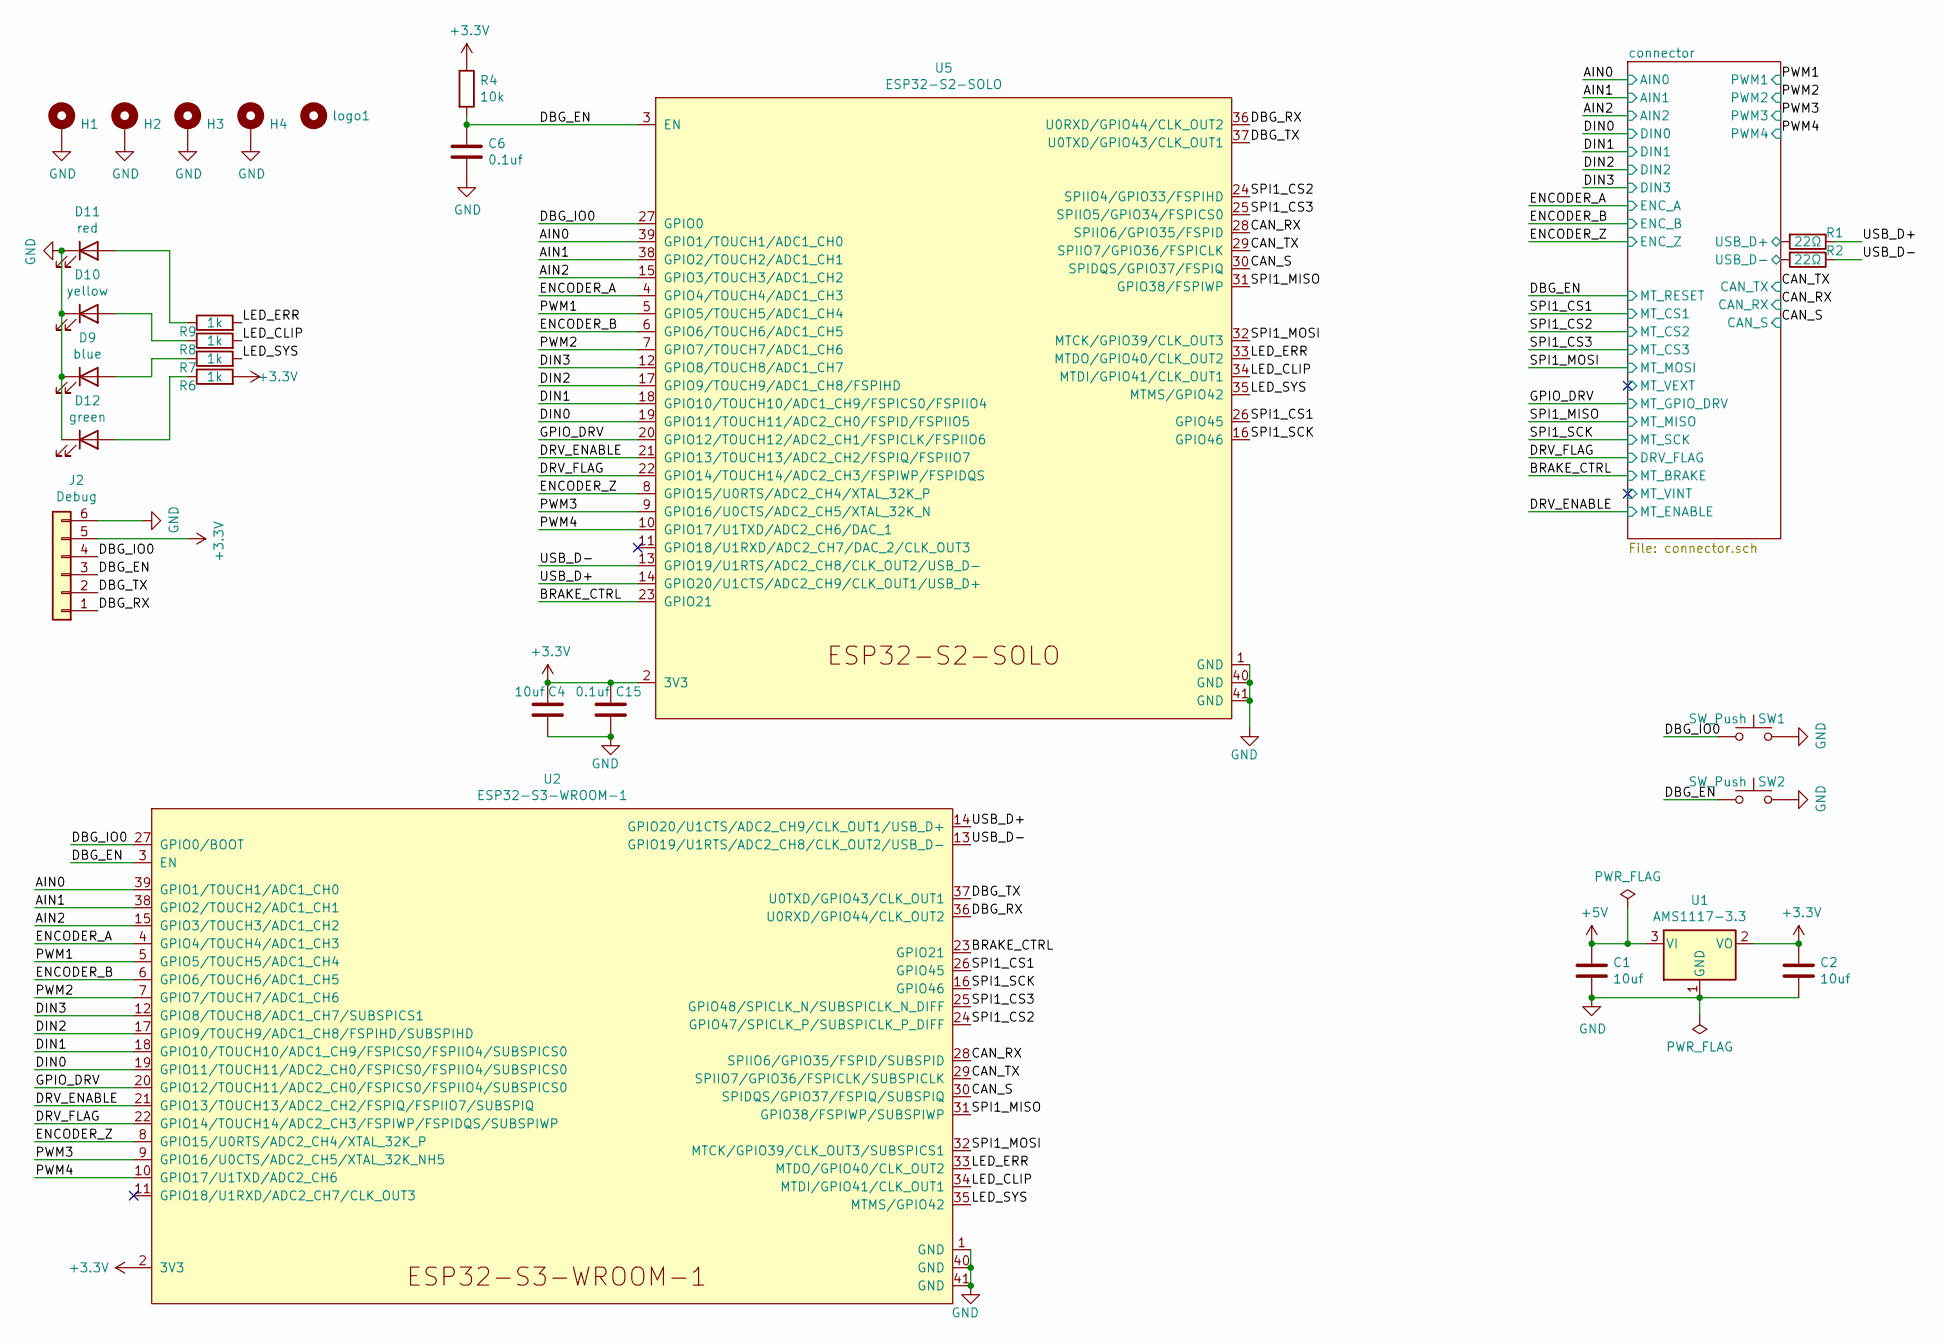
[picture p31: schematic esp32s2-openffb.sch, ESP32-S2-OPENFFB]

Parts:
C1, C2, C4: 10uf; C_0603_1608Metric
C6, C15: 0.1uf; C_0402_1005Metric
D9: blue; LED_0603_1608Metric
D10: yellow; LED_0603_1608Metric
D11: red; LED_0603_1608Metric
D12: green; LED_0603_1608Metric
H1, H2, H3, H4: MountingHole_Pad; MountingHole_3.2mm_M3_Pad_Via
J2: Debug; PinHeader_1x06_P2.54mm_Vertical
R1, R2: 22Ω; R_0402_1005Metric
R4: 10k; R_0402_1005Metric
R6, R7, R8, R9: 1k; R_0402_1005Metric
SW1, SW2: SW_Push; SW_SPST_EVPBF
U1: AMS1117-3.3; SOT-223-3_TabPin2
U2: ESP32-S3-WROOM-1
U5: ESP32-S2-SOLO
logo1: logo; OSHW-Logo2_9.8x8mm_SilkScreen

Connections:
+3V3: C2.2, C4.1, C15.1, J2.5, R4.1, R6.2, U1.2 (VO), U2.2 (3V3), U5.2 (3V3); also elsewhere on the board
+5V: C1.2, U1.3 (VI); also elsewhere on the board
/AIN0: U2.39 (GPIO1/TOUCH1/ADC1_CH0), U5.39 (GPIO1/TOUCH1/ADC1_CH0); also elsewhere on the board
/AIN1: U2.38 (GPIO2/TOUCH2/ADC1_CH1), U5.38 (GPIO2/TOUCH2/ADC1_CH1); also elsewhere on the board
/AIN2: U2.15 (GPIO3/TOUCH3/ADC1_CH2), U5.15 (GPIO3/TOUCH3/ADC1_CH2); also elsewhere on the board
/BRAKE_CTRL: U2.23 (GPIO21), U5.23 (GPIO21); also elsewhere on the board
/CAN_RX: U2.28 (SPIIO6/GPIO35/FSPID/SUBSPID), U5.28 (SPIIO6/GPIO35/FSPID); also elsewhere on the board
/CAN_S: U2.30 (SPIDQS/GPIO37/FSPIQ/SUBSPIQ), U5.30 (SPIDQS/GPIO37/FSPIQ); also elsewhere on the board
/CAN_TX: U2.29 (SPIIO7/GPIO36/FSPICLK/SUBSPICLK), U5.29 (SPIIO7/GPIO36/FSPICLK); also elsewhere on the board
/DBG_EN: C6.1, J2.3, R4.2, SW2.1, U2.3 (EN), U5.3 (EN); also elsewhere on the board
/DBG_IO0: J2.4, SW1.1, U2.27 (GPIO0/BOOT), U5.27 (GPIO0)
/DBG_RX: J2.1, U2.36 (U0RXD/GPIO44/CLK_OUT2), U5.36 (U0RXD/GPIO44/CLK_OUT2)
/DBG_TX: J2.2, U2.37 (U0TXD/GPIO43/CLK_OUT1), U5.37 (U0TXD/GPIO43/CLK_OUT1)
/DIN0: U2.19 (GPIO11/TOUCH11/ADC2_CH0/FSPICS0/FSPIIO4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), U5.19 (GPIO11/TOUCH11/ADC2_CH0/FSPID/FSPIIO5); also elsewhere on the board
/DIN1: U2.18 (GPIO10/TOUCH10/ADC1_CH9/FSPICS0/FSPIIO4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), U5.18 (GPIO10/TOUCH10/ADC1_CH9/FSPICS0/FSPIIO4); also elsewhere on the board
/DIN2: U2.17 (GPIO9/TOUCH9/ADC1_CH8/FSPIHD/SUBSPIHD), U5.17 (GPIO9/TOUCH9/ADC1_CH8/FSPIHD); also elsewhere on the board
/DIN3: U2.12 (GPIO8/TOUCH8/ADC1_CH7/SUBSPICS1), U5.12 (GPIO8/TOUCH8/ADC1_CH7); also elsewhere on the board
/DRV_ENABLE: U2.21 (GPIO13/TOUCH13/ADC2_CH2/FSPIQ/FSPIIO7/S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), U5.21 (GPIO13/TOUCH13/ADC2_CH2/FSPIQ/FSPIIO7); also elsewhere on the board
/DRV_FLAG: U2.22 (GPIO14/TOUCH14/ADC2_CH3/FSPIWP/FSPIDQS/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), U5.22 (GPIO14/TOUCH14/ADC2_CH3/FSPIWP/FSPIDQS); also elsewhere on the board
/ENCODER_A: U2.4 (GPIO4/TOUCH4/ADC1_CH3), U5.4 (GPIO4/TOUCH4/ADC1_CH3); also elsewhere on the board
/ENCODER_B: U2.6 (GPIO6/TOUCH6/ADC1_CH5), U5.6 (GPIO6/TOUCH6/ADC1_CH5); also elsewhere on the board
/ENCODER_Z: U2.8 (GPIO15/U0RTS/ADC2_CH4/XTAL_32K_P), U5.8 (GPIO15/U0RTS/ADC2_CH4/XTAL_32K_P); also elsewhere on the board
/GPIO_DRV: U2.20 (GPIO12/TOUCH11/ADC2_CH0/FSPICS0/FSPIIO4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), U5.20 (GPIO12/TOUCH12/ADC2_CH1/FSPICLK/FSPIIO6); also elsewhere on the board
/LED_CLIP: R8.2, U2.34 (MTDI/GPIO41/CLK_OUT1), U5.34 (MTDI/GPIO41/CLK_OUT1)
/LED_ERR: R9.2, U2.33 (MTDO/GPIO40/CLK_OUT2), U5.33 (MTDO/GPIO40/CLK_OUT2)
/LED_SYS: R7.2, U2.35 (MTMS/GPIO42), U5.35 (MTMS/GPIO42)
/PWM1: U2.5 (GPIO5/TOUCH5/ADC1_CH4), U5.5 (GPIO5/TOUCH5/ADC1_CH4); also elsewhere on the board
/PWM2: U2.7 (GPIO7/TOUCH7/ADC1_CH6), U5.7 (GPIO7/TOUCH7/ADC1_CH6); also elsewhere on the board
/PWM3: U2.9 (GPIO16/U0CTS/ADC2_CH5/XTAL_32K_NH5), U5.9 (GPIO16/U0CTS/ADC2_CH5/XTAL_32K_N); also elsewhere on the board
/PWM4: U2.10 (GPIO17/U1TXD/ADC2_CH6), U5.10 (GPIO17/U1TXD/ADC2_CH6/DAC_1); also elsewhere on the board
/SPI1_CS1: U2.26 (GPIO45), U5.26 (GPIO45); also elsewhere on the board
/SPI1_CS2: U2.24 (GPIO47/SPICLK_P/SUBSPICLK_P_DIFF), U5.24 (SPIIO4/GPIO33/FSPIHD); also elsewhere on the board
/SPI1_CS3: U2.25 (GPIO48/SPICLK_N/SUBSPICLK_N_DIFF), U5.25 (SPIIO5/GPIO34/FSPICS0); also elsewhere on the board
/SPI1_MISO: U2.31 (GPIO38/FSPIWP/SUBSPIWP), U5.31 (GPIO38/FSPIWP); also elsewhere on the board
/SPI1_MOSI: U2.32 (MTCK/GPIO39/CLK_OUT3/SUBSPICS1), U5.32 (MTCK/GPIO39/CLK_OUT3); also elsewhere on the board
/SPI1_SCK: U2.16 (GPIO46), U5.16 (GPIO46); also elsewhere on the board
/USB_D+: R1.1, U2.14 (GPIO20/U1CTS/ADC2_CH9/CLK_OUT1/USB_D+), U5.14 (GPIO20/U1CTS/ADC2_CH9/CLK_OUT1/USB_D+)
/USB_D-: R2.1, U2.13 (GPIO19/U1RTS/ADC2_CH8/CLK_OUT2/USB_D-), U5.13 (GPIO19/U1RTS/ADC2_CH8/CLK_OUT2/USB_D-)
/connector/USB_D+: R1.2; also elsewhere on the board
/connector/USB_D-: R2.2; also elsewhere on the board
GND: C1.1, C2.1, C4.2, C6.2, C15.2, D9.1 (K), D10.1 (K), D11.1 (K), D12.1 (K), H1.1, H2.1, H3.1, H4.1, J2.6, SW1.2, SW2.2, U1.1 (GND), U2.1 (GND), U2.40 (GND), U2.41 (GND), U5.1 (GND), U5.40 (GND), U5.41 (GND); also elsewhere on the board
unnamed: D9.2 (A), R7.1
unnamed: D10.2 (A), R8.1
unnamed: D11.2 (A), R9.1
unnamed: D12.2 (A), R6.1

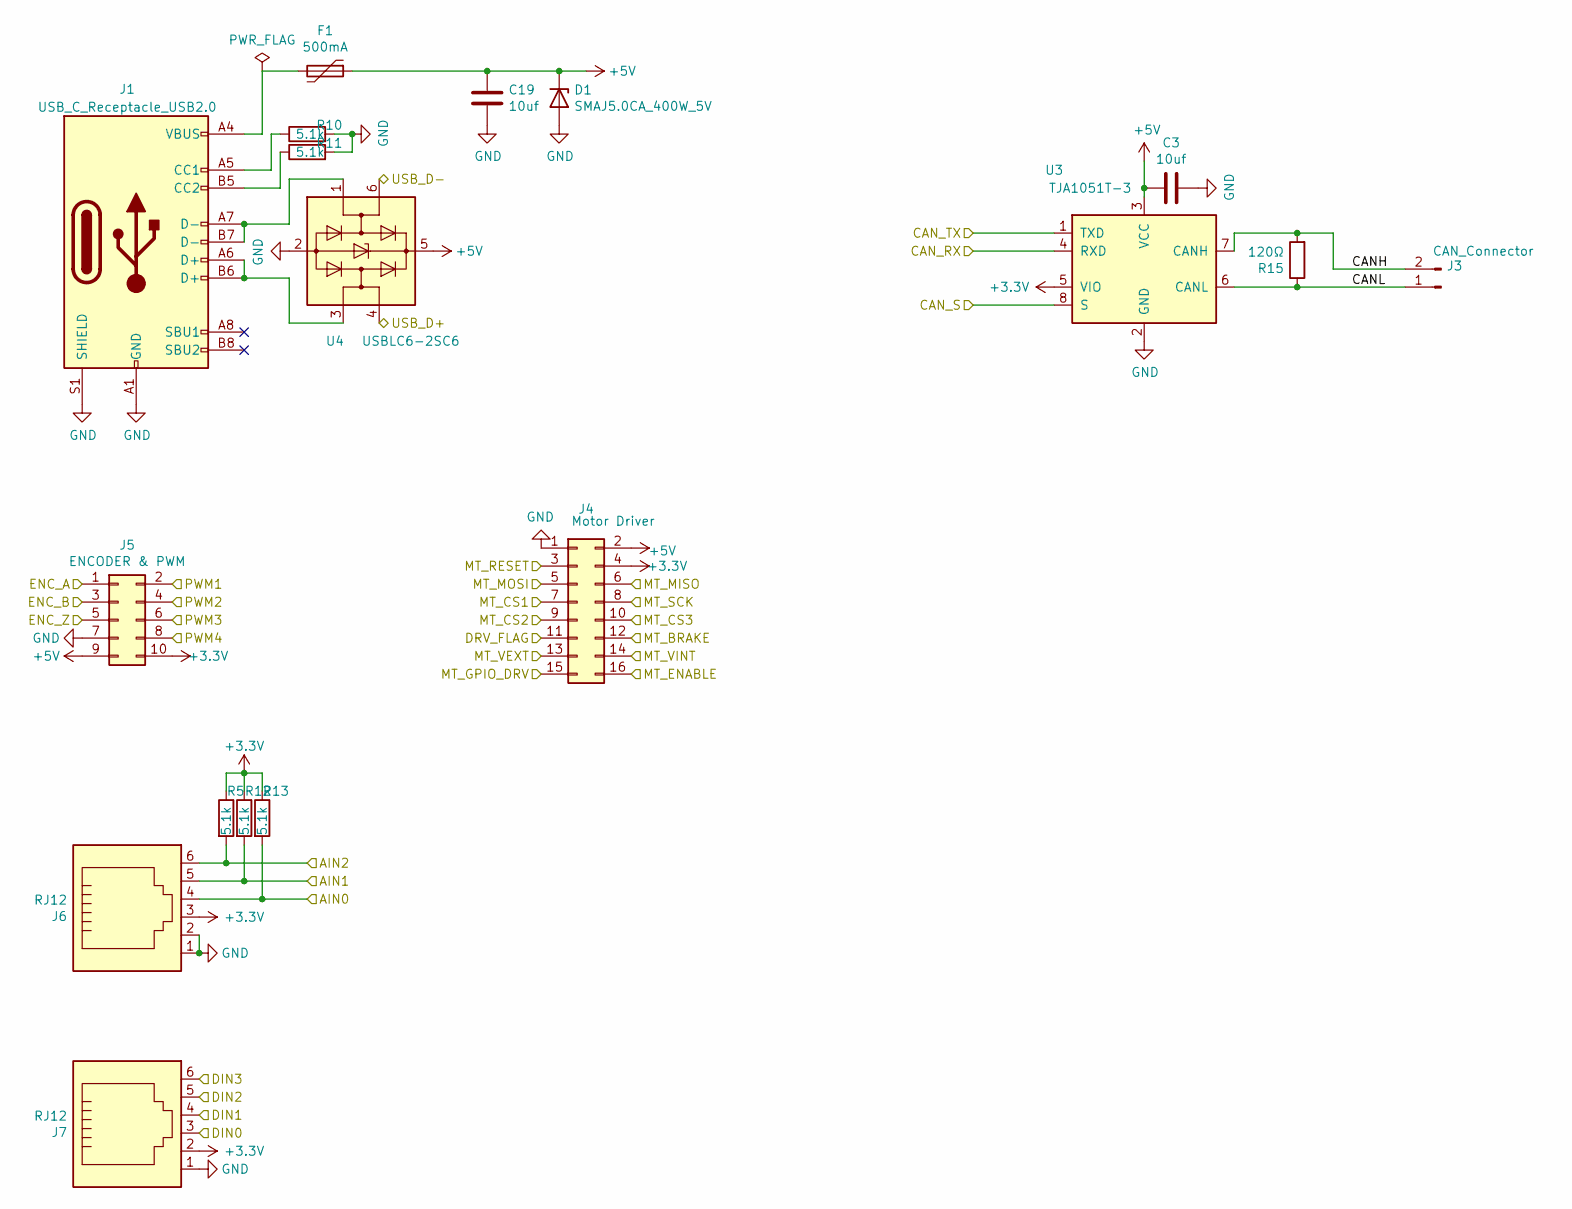
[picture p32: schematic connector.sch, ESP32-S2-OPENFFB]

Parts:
C3, C19: 10uf; C_0603_1608Metric
D1: SMAJ5.0CA_400W_5V; D_SMA
F1: 500mA; Fuse_0805_2012Metric
J1: USB_C_Receptacle_USB2.0; USB_C_Receptacle_Palconn_UTC16-G
J3: CAN_Connector; PinHeader_1x02_P2.54mm_Vertical
J4: Motor Driver; PinHeader_2x08_P2.54mm_Vertical
J5: ENCODER & PWM; PinHeader_2x05_P2.54mm_Vertical
J6, J7: RJ12; RJ25_Wayconn_MJEA-660X1_Horizontal
R5, R10, R11, R12, R13: 5.1k; R_0402_1005Metric
R15: 120Ω; R_0603_1608Metric
U3: TJA1051T-3; SOIC-8_3.9x4.9mm_P1.27mm
U4: USBLC6-2SC6; SOT-23-6

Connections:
+3V3: J4.4, J5.10, J6.3, J7.2, R5.1, R12.1, R13.1, U3.5 (VIO); also elsewhere on the board
+5V: C3.2, C19.2, D1.1 (A1), F1.1, J4.2, J5.9, U3.3 (VCC), U4.5 (VBUS); also elsewhere on the board
/AIN0: J6.4, R13.2; also elsewhere on the board
/AIN1: J6.5, R12.2; also elsewhere on the board
/AIN2: J6.6, R5.2; also elsewhere on the board
/BRAKE_CTRL: J4.12; also elsewhere on the board
/CAN_RX: U3.4 (RXD); also elsewhere on the board
/CAN_S: U3.8 (S); also elsewhere on the board
/CAN_TX: U3.1 (TXD); also elsewhere on the board
/DBG_EN: J4.3; also elsewhere on the board
/DIN0: J7.3; also elsewhere on the board
/DIN1: J7.4; also elsewhere on the board
/DIN2: J7.5; also elsewhere on the board
/DIN3: J7.6; also elsewhere on the board
/DRV_ENABLE: J4.16; also elsewhere on the board
/DRV_FLAG: J4.11; also elsewhere on the board
/ENCODER_A: J5.1; also elsewhere on the board
/ENCODER_B: J5.3; also elsewhere on the board
/ENCODER_Z: J5.5; also elsewhere on the board
/GPIO_DRV: J4.15; also elsewhere on the board
/PWM1: J5.2; also elsewhere on the board
/PWM2: J5.4; also elsewhere on the board
/PWM3: J5.6; also elsewhere on the board
/PWM4: J5.8; also elsewhere on the board
/SPI1_CS1: J4.7; also elsewhere on the board
/SPI1_CS2: J4.9; also elsewhere on the board
/SPI1_CS3: J4.10; also elsewhere on the board
/SPI1_MISO: J4.6; also elsewhere on the board
/SPI1_MOSI: J4.5; also elsewhere on the board
/SPI1_SCK: J4.8; also elsewhere on the board
/connector/CANH: J3.2, R15.2, U3.7 (CANH)
/connector/CANL: J3.1, R15.1, U3.6 (CANL)
/connector/USB_D+: U4.4 (I/O2); also elsewhere on the board
/connector/USB_D-: U4.6 (I/O1); also elsewhere on the board
GND: C3.1, C19.1, D1.2 (A2), J1.A1 (GND), J1.A12 (GND), J1.B1 (GND), J1.B12 (GND), J1.S1 (SHIELD), J4.1, J5.7, J6.1, J6.2, J7.1, R10.2, R11.2, U3.2 (GND), U4.2 (GND); also elsewhere on the board
unnamed: F1.2, J1.A4 (VBUS), J1.A9 (VBUS), J1.B4 (VBUS), J1.B9 (VBUS)
unnamed: J1.A5 (CC1), R10.1
unnamed: J1.A6 (D+), J1.B6 (D+), U4.3 (I/O2)
unnamed: J1.A7 (D-), J1.B7 (D-), U4.1 (I/O1)
unnamed: J1.B5 (CC2), R11.1

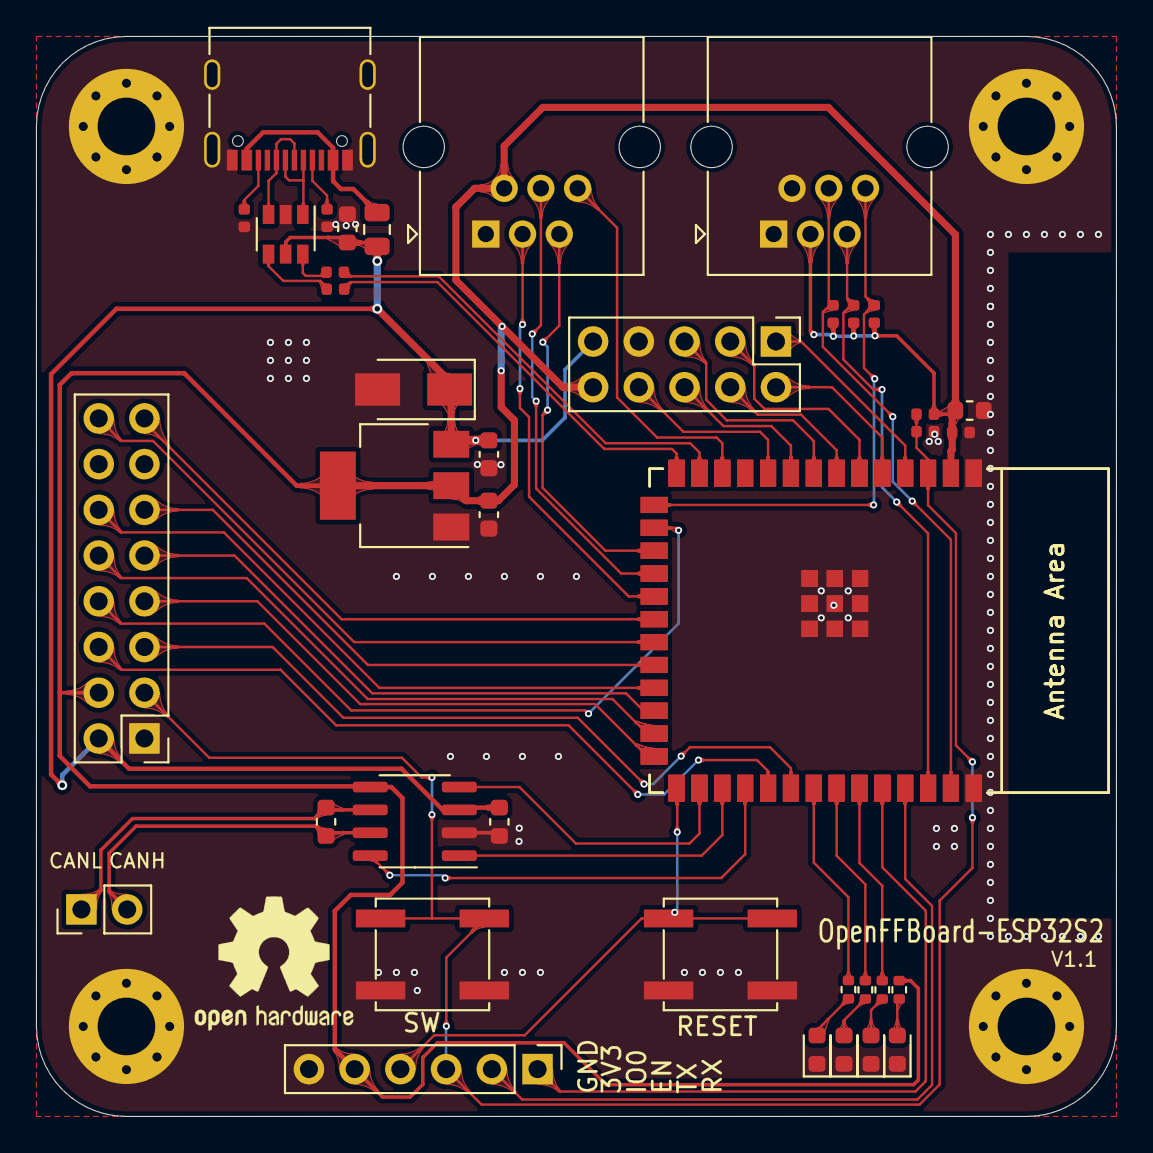
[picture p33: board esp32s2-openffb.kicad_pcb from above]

Board: 2 copper layers, 60.0 x 60.0 mm, 45 parts (0 on the bottom side), 52 nets.

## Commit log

2022-04-30 add vesc and docs
    [USB_Type_C_6pin.STEP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]
2022-04-30 update vesc to v1.2
    [brake_board-Bottom_Cu.gbr, brake_board-Bottom_Mask.gbr, brake_board-Bottom_Paste.gbr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]
2022-09-02 add structual parts
    [4080-aluminum-profile-1m.SLDPRT, M3螺丝-7.6mm.SLDPRT, M3螺帽.SLDPRT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]
2022-09-05 update simple-bldc board
    [simple_bldc-Bottom_Cu.gbr, simple_bldc-Bottom_Mask.gbr, simple_bldc-Bottom_Paste.gbr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]
2024-07-15 Structural_parts: add ver4
    [AC Servo motor 90ST-M04025 v1.SLDASM, AC Servo motor 90ST-M04025 v1.SLDPRT, esp32s2-openffb.SLDPRT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]
